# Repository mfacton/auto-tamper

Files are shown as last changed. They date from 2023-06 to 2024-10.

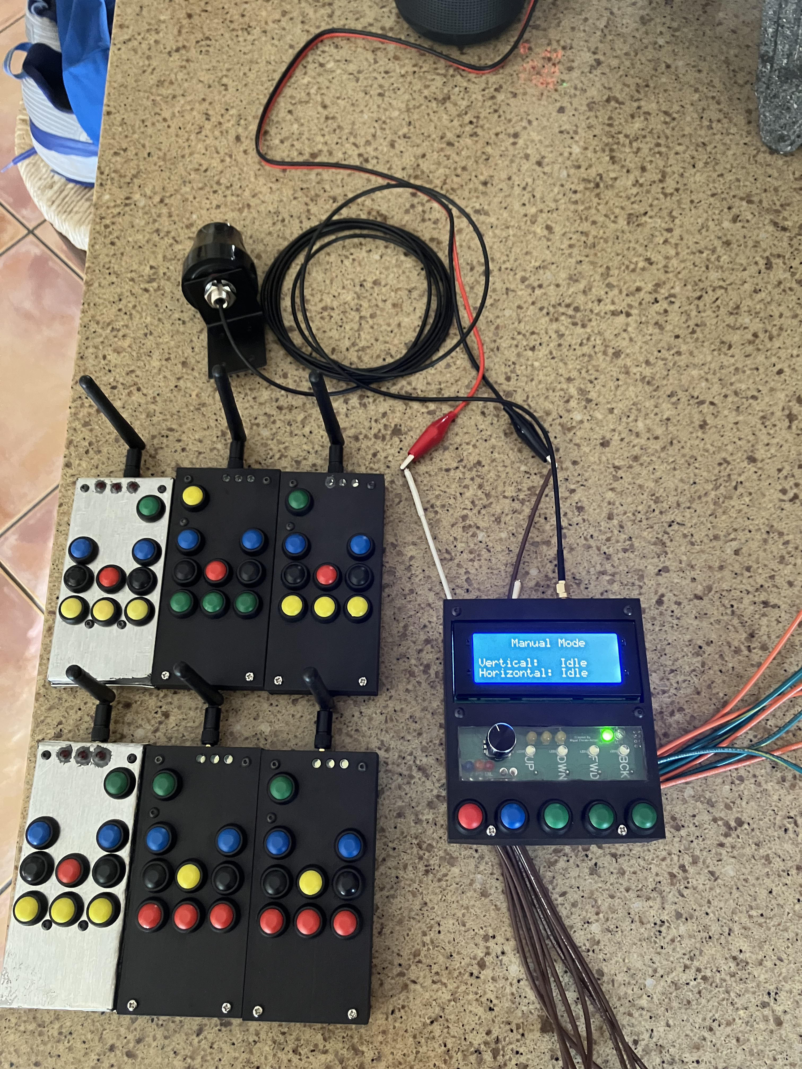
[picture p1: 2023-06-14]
project.jpg

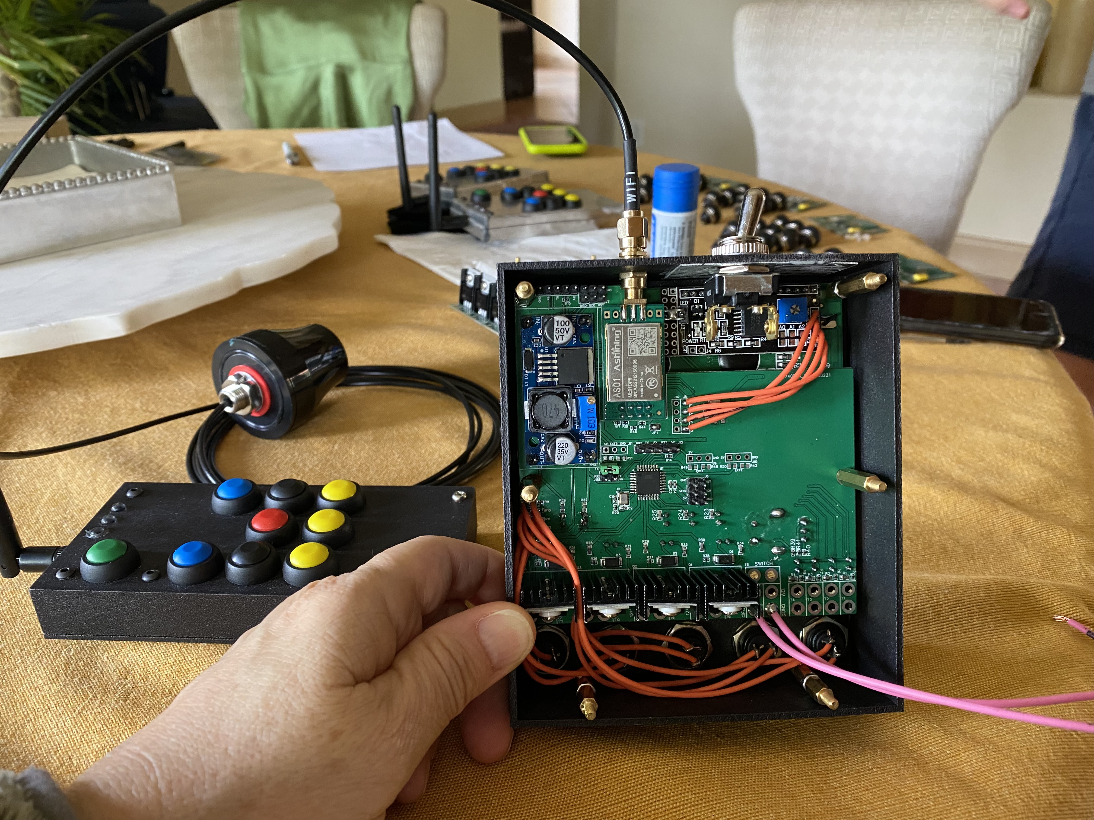
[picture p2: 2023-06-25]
system3/module.jpg

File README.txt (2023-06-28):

This is an autotamper system which includes a module that can be installed onto a module builder as well as remotes for long distance control.
The buttons on the module builder are in order STOP, EDIT, PROG1, PROG2, PROG3

NOTE:
Circuit board files are json files which are openable through the EasyEDA design software.
Both SPI and UART can be accomplished using an Arduino Uno board.
To use SPI, connect pins GND, 3.3V, 10-RESET, 11-MOSI, 12-MISO, 13-CLK.
Also use a voltage Bi-Directional Logic Level Converter so the 5V Arduino Uno signals will not harm the 3V circuit.
To use UART, remove the DIP chip from the Arduino Uno and connect GND, 5V, RESET-RESET, RX-RX, TX-TX.

Remote NOTES:
For remote_v3, install MiniCore on the Arduino IDE, then select the Board: ATMega328, BOD 2.7V, No Bootloader, Extrnal 8MHz Clock, LTO Enabled, Variant 328P/328PA, then to upload program, Sketch -> Upload Using Programmer
For remote_v3, the program can be uploaded using the 6 SPI pins, no bootloader required.
For remote_v2, it is necessary to burn the bootloader before soldering the jumper connector near the transmitter.
Afterwards, a program can be uploaded using the UART pins (5V, RESET, RX, TX, GND).

Module NOTES:
Chip A is located near the center of the board and chip B is located underneath the 12V to 5V voltage regulator.
For the module, it is necessary to burn the bootloader on both ATMega328p-au chips before soldering the jumper connector near the transmitter.
To program the chips, use the 5 UART pins and ensure the RX and TX pins between chips A and B are not connected.
After both chips A and B are programmed, you need to jumper or solder the RX pin of chip A to the TX pin of chip B for them to communicate.

Module Wiring:
12V and GND power the module.
There are 4 sensors, F1: the feeler near the cab, F2: the feeler far from the cab, PS: the pressure sensor, and OIL: the low oil switch.
For the four sensors there is a + and - wire, but it shouldn't matter which way it is connected.
There are also 4 coils which control fwd, back, up, down, each having +/- and the polarity doesn't matter.

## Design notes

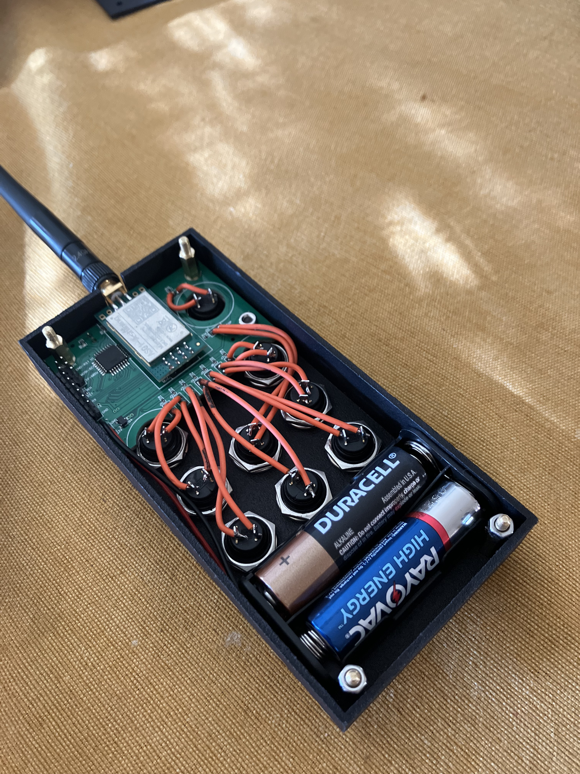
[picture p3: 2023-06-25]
system3/remote_v3/remote.jpg

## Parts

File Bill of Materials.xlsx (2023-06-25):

ITEM | Module | Remote x8 | Source | Unit Price | Total Price
I2C LCD Screen | 1 | 0 | Amazon (https://www.amazon.com/ALMOCN-Display-Interface-Backlight-MEGA2560/dp/B08Z74MSG1) | 8 | 8
5A Inline Fuse | 1 | 0 | Amazon (https://www.amazon.com/HUIQIAODS-Holder-Waterproof-Pigtail-Inline/dp/B08BLHCJBC) | 4 | 4
LEDs | 13 | 3(24) | Amazon (https://www.amazon.com/eBoot-Pieces-Emitting-Diodes-Assorted/dp/B06XPV4CSH) | 0.08 | 2.96
Pin Headers | 22 | 6(48) | Amazon (https://www.amazon.com/Jabinco-Breakable-Header-Connector-Arduino/dp/B0817JG3XN) | 0.01 | 0.7
Buck Regulators | 1 | 0 | Amazon (https://www.amazon.com/Valefod-Efficiency-Voltage-Regulator-Converter/dp/B076H3XHXP) | 1.83 | 1.83
Ceramic Capacitors | 2 | 2(16) | Amazon (https://www.amazon.com/BOJACK-Ceramic-Capacitor-Assortment-Capacitors/dp/B07P8N8BW9) | 0.03 | 0.54
Mosfets | 4 | 0 | Amazon (https://www.amazon.com/BOJACK-IRF520-Transistors-IRF520N-N-Channel/dp/B082J3FNJS) | 0.8 | 3.2
Diodes | 4 | 0 | Amazon (https://www.amazon.com/BOJACK-Schottky-DO-201AD-Electronic-Silicon/dp/B07Q4HYL1P) | 0.24 | 0.96
Buttons | 5 | 9(72) | Amazon (https://www.amazon.com/Waterproof-Momentary-Button-Switch-Colors/dp/B07F24Y1TB) | 0.67 | 51.59
Transcievers | 1 | 1(8) | Amazon (https://www.amazon.com/MakerFocus-nRF24L01P-Transmission-Interface-Anti-Interference/dp/B07QC1SXJ8) | 8.5 | 76.5
Antenna | 1 | 0 | Amazon (https://www.amazon.com/Waterproof-Omni-Directional-Repeater-Wireless-Security/dp/B095JTSQ58) | 15.99 | 15.99
Plexi Glass | 1 | 0 | Ace Hardware | x | x
Rotary Encoder | 1 | 0 | Amazon (https://www.amazon.com/Cylewet-Encoder-Digital-Potentiometer-Arduino/dp/B07DM2YMT4) | 1.78 | 1.78
Switch | 1 | 0 | Ace Hardware | 5.99 | 5.99
Module Circuit | 1 | 0 | JLCPCB (https://jlcpcb.com/) | 24.94 | 24.94
Remote Circuit | 0 | 1(5) | JLCPCB (https://jlcpcb.com/) | 6.14 | 32.06
Module 3D prints | 1 | 0 | JLCPCB (https://3d.jlcpcb.com/) | 32.16 | 32.16
Remote 3D prints | 0 | 5 | JLCPCB (https://3d.jlcpcb.com/) | 21.52 | 107.61
JLCPCB Shipping Total |  |  |  |  | 72.18
M3 Long Bolts | 4 | 3(24) | Ace Hardware | 0.64 | 18
M3 Offsets |  |  | Amazon (https://www.amazon.com/Csdtylh-Male-Female-Standoff-Stainless-Assortment/dp/B06Y5TJXY1) |  | 13.88
Module Duplicate | 1 |  |  | 105.79 | 105.79
Extra Cost = total spent(including old module) - cost per units |  |  |  |  | 250.13
Total |  |  |  |  | 798.63

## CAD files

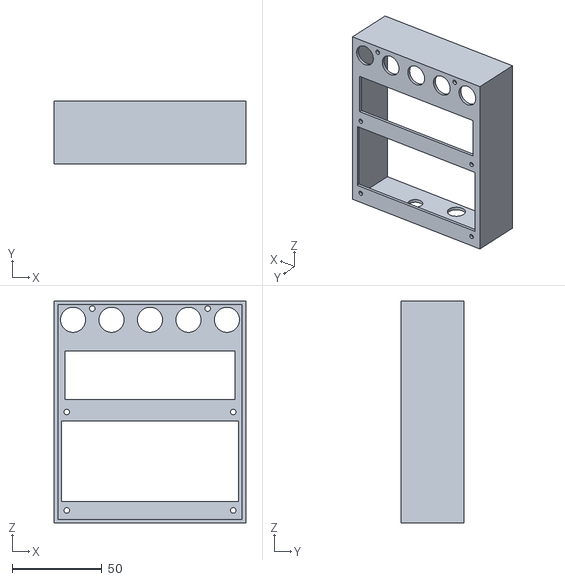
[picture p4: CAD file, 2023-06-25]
system3/module_body.stl
107.0 x 35.0 x 124.0

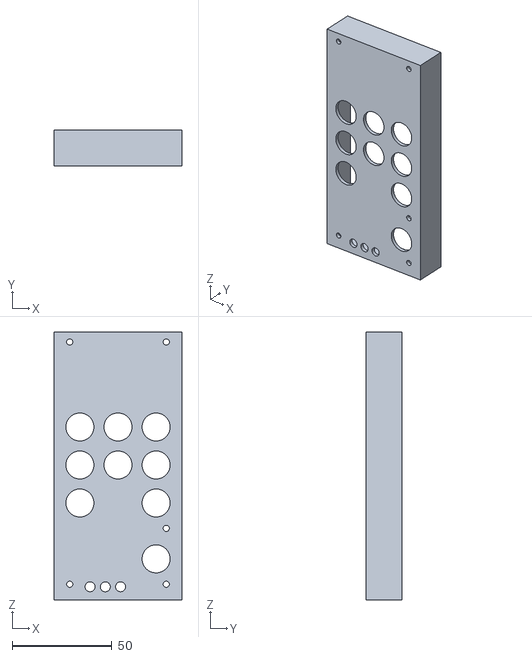
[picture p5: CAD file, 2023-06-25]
system3/remote_v3/remote_body.stl
64.0 x 18.0 x 134.0

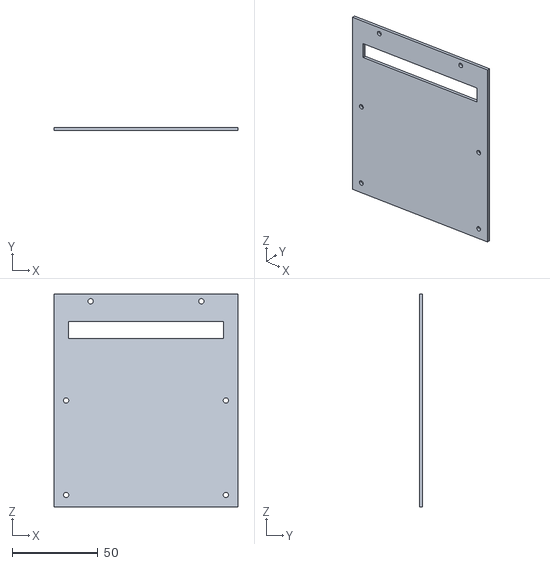
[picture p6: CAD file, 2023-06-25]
system3/module_lid.stl
107.0 x 2.00 x 124.0

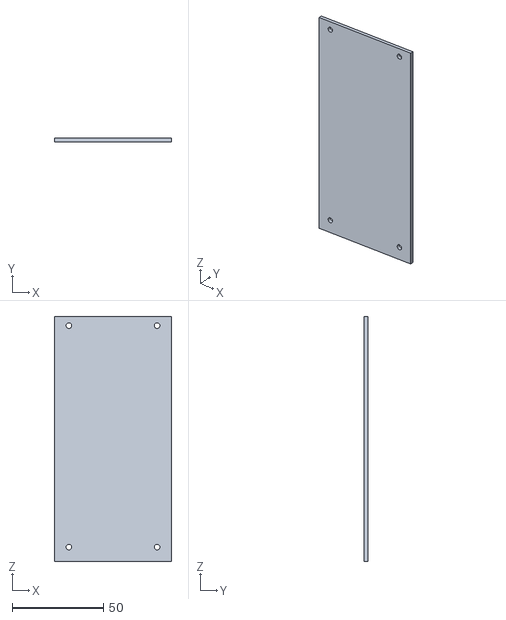
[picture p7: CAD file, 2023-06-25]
system3/remote_v3/remote_lid.stl
64.0 x 2.00 x 134.0

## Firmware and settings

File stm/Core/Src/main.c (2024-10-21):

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
/* Includes ------------------------------------------------------------------*/
#include "main.h"
#include "usb_device.h"

/* USER CODE BEGIN Includes */
#include "modules/movement.h"
#include "modules/input.h"
#include "modules/sensor.h"
#include "modules/memory.h"
#include "modules/display.h"
#include "modules/receiver.h"
#include "modules/LED.h"
#include "control.h"
/* USER CODE END Includes */

I2C_HandleTypeDef hi2c2;

SPI_HandleTypeDef hspi2;

TIM_HandleTypeDef htim2;
TIM_HandleTypeDef htim3;

UART_HandleTypeDef huart1;

void SystemClock_Config(void);
static void MX_GPIO_Init(void);
static void MX_I2C2_Init(void);
static void MX_SPI2_Init(void);
static void MX_USART1_UART_Init(void);
static void MX_TIM2_Init(void);
static void MX_TIM3_Init(void);
/**
  * @brief  The application entry point.
  * @retval int
  */
int main(void)
{
  /* MCU Configuration--------------------------------------------------------*/

  /* Reset of all peripherals, Initializes the Flash interface and the Systick. */
  HAL_Init();

  /* Configure the system clock */
  SystemClock_Config();

  /* Initialize all configured peripherals */
  MX_GPIO_Init();
  MX_I2C2_Init();
  MX_SPI2_Init();
  MX_USART1_UART_Init();
  MX_USB_DEVICE_Init();
  MX_TIM2_Init();
  MX_TIM3_Init();
  /* USER CODE BEGIN 2 */

	HAL_Delay(200);

	Movement_Init();
	Input_Init();
	Sensor_Init();
	Memory_Init(&hi2c2);
	Receiver_Init(&hspi2);
	Display_Init(&hi2c2);

	HAL_Delay(100);

	Control_Init();

  /* USER CODE END 2 */

  /* Infinite loop */
  /* USER CODE BEGIN WHILE */
	while (1) {
		Control_Loop();
    /* USER CODE END WHILE */

    /* USER CODE BEGIN 3 */
	}
  /* USER CODE END 3 */
}

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
/* USER CODE BEGIN 4 */
//every 10 milliseconds
void HAL_TIM_PeriodElapsedCallback(TIM_HandleTypeDef *htim) {
	if (htim == &htim2) {
		Input_Handler();//every 10 milliseconds
	}else{//tim3
		Sensor_Handler_tim();//every 400 microseconds
	}
}

void HAL_GPIO_EXTI_Callback(uint16_t GPIO_Pin) {
	if (GPIO_Pin == NRF_IRQ_Pin) {
		Receiver_Handler();
	}
	else {
		Sensor_Handler_irq(GPIO_Pin);
	}
}
/* USER CODE END 4 */
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


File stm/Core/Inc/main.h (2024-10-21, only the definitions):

#define RE_SW_Pin GPIO_PIN_13
#define RE_SW_GPIO_Port GPIOC
#define RE_CLK_Pin GPIO_PIN_14
#define RE_CLK_GPIO_Port GPIOC
#define RE_DT_Pin GPIO_PIN_15
#define RE_DT_GPIO_Port GPIOC
#define BTN_PRG1_Pin GPIO_PIN_0
#define BTN_PRG1_GPIO_Port GPIOA
#define BTN_STOP_Pin GPIO_PIN_1
#define BTN_STOP_GPIO_Port GPIOA
#define BTN_PRG3_Pin GPIO_PIN_2
#define BTN_PRG3_GPIO_Port GPIOA
#define BTN_PRG2_Pin GPIO_PIN_3
#define BTN_PRG2_GPIO_Port GPIOA
#define BTN_EDIT_Pin GPIO_PIN_4
#define BTN_EDIT_GPIO_Port GPIOA
#define LED_PRG3_Pin GPIO_PIN_5
#define LED_PRG3_GPIO_Port GPIOA
#define LED_PRG2_Pin GPIO_PIN_6
#define LED_PRG2_GPIO_Port GPIOA
#define LED_PRG1_Pin GPIO_PIN_7
#define LED_PRG1_GPIO_Port GPIOA
#define LED_EDIT_Pin GPIO_PIN_0
#define LED_EDIT_GPIO_Port GPIOB
#define NRF_IRQ_Pin GPIO_PIN_1
#define NRF_IRQ_GPIO_Port GPIOB
#define NRF_IRQ_EXTI_IRQn EXTI1_IRQn
#define BOOT1_Pin GPIO_PIN_2
#define BOOT1_GPIO_Port GPIOB
#define NRF_CSN_Pin GPIO_PIN_12
#define NRF_CSN_GPIO_Port GPIOB
#define NRF_CE_Pin GPIO_PIN_8
#define NRF_CE_GPIO_Port GPIOA
#define DBG_TX_Pin GPIO_PIN_9
#define DBG_TX_GPIO_Port GPIOA
#define DBG_RX_Pin GPIO_PIN_10
#define DBG_RX_GPIO_Port GPIOA
#define SIG1_Pin GPIO_PIN_15
#define SIG1_GPIO_Port GPIOA
#define SIG2_Pin GPIO_PIN_3
#define SIG2_GPIO_Port GPIOB
#define SIG3_Pin GPIO_PIN_4
#define SIG3_GPIO_Port GPIOB
#define SIG4_Pin GPIO_PIN_5
#define SIG4_GPIO_Port GPIOB
#define FL1_Pin GPIO_PIN_6
#define FL1_GPIO_Port GPIOB
#define FL1_EXTI_IRQn EXTI9_5_IRQn
#define FL2_Pin GPIO_PIN_7
#define FL2_GPIO_Port GPIOB
#define FL2_EXTI_IRQn EXTI9_5_IRQn
#define PS_Pin GPIO_PIN_8
#define PS_GPIO_Port GPIOB
#define PS_EXTI_IRQn EXTI9_5_IRQn
#define OIL_Pin GPIO_PIN_9
#define OIL_GPIO_Port GPIOB
#define OIL_EXTI_IRQn EXTI9_5_IRQn

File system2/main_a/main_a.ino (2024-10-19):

#include <EEPROM.h>
#include <Wire.h>
#include <LiquidCrystal_I2C.h>

bool editMode = false;
bool autoMode = false;
//independent module
//functions that read sensor inputs
namespace sensors {
  inline void init() {
    DDRD &= 0b11100011;
    DDRC &= 0b11111110;
  }
  inline bool pressure() { //D3
    return !((PIND >> 3)&1);
  }
  bool feeler(uint8_t number) {
    if (number == 0) {//feeler 1
      return !(PINC&1); //C0
    }else{//feeler 2
      return !((PIND>>2)&1); //D2
    }
  }
  inline bool oil() { //D4
    return !((PIND>>4)&1);
  }
}
//independent module
//functions that control movement
namespace movement {
  //coil1 B0 UP
  //coil2 D7 DOWN
  //coil3 D6 FWD
  //coil4 D5 BACK
  inline void init() {
    DDRB |= 0b00000001;
    DDRD |= 0b11100000;
  }
  // bool moving() {
  //   return (PORTD>>5) > 0 || (PORTB&1);
  // }
  inline void up() {
    PORTD &= 0b01111111;
    PORTB |= 0b00000001;
  }
  inline void down() {
    PORTD |= 0b10000000;
    PORTB &= 0b11111110;
  }
  inline void stopUD() {
    PORTB &= 0b11111110;
    PORTD &= 0b01111111;
  }
  inline void forward() {
    PORTD &= 0b11011111;
    PORTD |= 0b01000000;
  }
  inline void backward() {
    PORTD |= 0b00100000;
    PORTD &= 0b10111111;
  }
  void moveFB(uint8_t direction) {
    if (direction) {
      forward();
    }else{
      backward();
    }
  }
  inline void stopFB() {
    PORTD &= 0b10011111;
  }
  inline void stopAll() {
    PORTD &= 0b00011111;
    PORTB &= 0b11111110;
  }
}
//independent module
//functions that control program LEDs
namespace LEDs {
  inline void init() {
    DDRC |= 0b00000010;
    DDRB |= 0b00000110;
  }

  inline void clear() {
    PORTC &= 0b11111101;
    PORTB &= 0b11111001;
  }

  inline void set(uint8_t led) {
    switch (led) {
      case 1: //C1
        PORTC |= 0b00000010;
        break;
      case 2: //B2
        PORTB |= 0b00000100;
        break;
      case 3: //B1
        PORTB |= 0b00000010;
        break;
    }
  }
}
//independent module
//declares some memory locations
//functions that abstract memory managment
namespace mem {
  //0-15 non-used
  //16-63 programs
  //64-127 individual

  constexpr uint8_t height = 0;
  constexpr uint8_t distance = 1;
  constexpr uint8_t delay = 2;
  constexpr uint8_t passes = 3;
  constexpr uint8_t safety = 4;

  uint16_t getVariable (uint8_t address) {
    const uint8_t mappedAddress = address<<1;
    return (EEPROM.read(mappedAddress) << 8) | EEPROM.read(mappedAddress|1);
  }

  void setVariable (uint8_t address, uint16_t value) {
    const uint8_t mappedAddress = address<<1;
    EEPROM.update(mappedAddress, value>>8);
    EEPROM.update(mappedAddress|1, value);
  }

  void reset() {
    for (uint16_t address = 0; address < 256; address++) {
      EEPROM.update(address, EEPROM.read(address+256));
    }
  }

  void setDefaults() {
    for (uint16_t address = 0; address < 256; address++) {
      EEPROM.update(address+256, EEPROM.read(address));
    }
  }
}
//independent module
//intitialize lcd and function to draw text
namespace lcd {
  namespace {
    constexpr char* blankLiteral = "                    ";//20 spaces
    LiquidCrystal_I2C lcd = LiquidCrystal_I2C(0x27, 20, 4);
  }

  inline void init() {
    lcd.init();
    lcd.backlight();
    lcd.noAutoscroll();
    lcd.cursor_off();
    lcd.blink_off();
    lcd.clear();
  }

  inline void print(char* text) {
    lcd.print(text);
  }

  void printText(uint8_t row, uint8_t col, char* text) {
    lcd.setCursor(col, row);
    lcd.print(text);
  }

  void printValue(uint16_t value) {
    char cstr[6];
    ltoa(value, cstr, 10);
    lcd.print(cstr);
    const uint8_t len = strlen(cstr);
    lcd.print(blankLiteral+len+15);
  }

  void printValue(uint8_t row, uint8_t col, uint16_t value) {
    lcd.setCursor(col, row);
    printValue(value);
  }

  inline void printTitle(char* text) {
    uint8_t len = strlen(text);
    printText(0, 10-len/2, text);
  }

  void printLine(uint8_t row, uint8_t col, char* text) {
    const uint8_t len = strlen(text);
    printText(row, col, text);
    const uint8_t start = col+len;
    lcd.print(blankLiteral+start);
  }

  inline void clear() {
    lcd.clear();
  }
}
//display control for edit mode
namespace edit {//7480 989
  namespace {
    constexpr uint16_t DOUBLE_PRESS_TIME = 200;

    constexpr char* scrollIncrements[3] = {"x1", "x50", "x1000"};
    constexpr char* menuLiterals[4] = {"Program 1", "Program 2", "Program 3", "General"};
    constexpr char* programLiterals[8] = {"Height", "Distance Time", "Bottom Delay", "Total Passes", "Safety Timeout", "BACK"};
    constexpr char* generalLiterals[3] = {"Reset", "Set As Default", "BACK"};
    constexpr char* confirmLiterals[2] = {"BACK", "Confirm"};

    constexpr uint8_t confirmRedirects[2] = {0, 0};

    struct page {
      const uint8_t optionLength;
      const uint8_t* redirects;
      const char* title;
      const char** options;
    };

    constexpr page menu = {4, (const uint8_t [4]){1,2,3,4}, "Menu", menuLiterals};
    constexpr page prog1 = {6, (const uint8_t[6]){16,17,18,19,20, 0}, menuLiterals[0], programLiterals};
    constexpr page prog2 = {6, (const uint8_t[6]){32,33,34,35,36, 0}, menuLiterals[1], programLiterals};
    constexpr page prog3 = {6, (const uint8_t[6]){48,49,50,51,52, 0}, menuLiterals[2], programLiterals};
    constexpr page general = {3, (const uint8_t[3]){5, 6, 0}, menuLiterals[3], generalLiterals};
    constexpr page reset = {2, confirmRedirects, generalLiterals[0], confirmLiterals};
    constexpr page setDefaults = {2, confirmRedirects, generalLiterals[1], confirmLiterals};

    constexpr page pages[7] = {
      menu,
      prog1,
      prog2,
      prog3,
      general,
      reset,
      setDefaults
    };

    //menu variables
    uint8_t pageNum;
    uint8_t select;//index of ">"
    uint8_t maxSelect;
    uint8_t view;//index of top selection option
    bool editValue;

    //temp value variables
    uint8_t address;
    uint16_t value;
    uint8_t scroll;//0,1,2 amount to change variable by x1 x50 x1000
    uint16_t increment;//1,50,1000 gets loaded based on "scroll" to save processing

    //-1 no press yet
    //double press to enter
    //single press to change scroll
    long lastPress;

    void initValue(uint8_t valueAddress) {
      editValue = true;
      address = valueAddress;
      value = mem::getVariable(address);
      scroll = 0;
      increment = 1;
      lastPress = 0;

      lcd::clear();
      lcd::printTitle(*(pages[pageNum].options+scroll));
      lcd::printText(1, 0, "Original:");
      lcd::printValue(1, 10, value);
      lcd::printText(2, 0, "Edited:");
      lcd::printValue(2, 8, value);
      lcd::printText(3, 0, "Increment:");
      lcd::printText(3, 11, scrollIncrements[0]);
    }
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

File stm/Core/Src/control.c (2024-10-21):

/*
 * control.c
 *
 *  Created on: Jul 5, 2023
 *      Author: mfact
 */

#include <modules/receiver.h>
#include "main.h"
#include "control.h"
#include "modules/sensor.h"
#include "modules/movement.h"
#include "modules/display.h"
#include "modules/input.h"
#include "modules/LED.h"
#include "modules/memory.h"
#include "modules/menu_config.h"

#include <stdio.h>

//mode variables
static uint8_t mode_edit;
static uint8_t mode_auto;

//buffer for variables in current program
static uint16_t running_variables[8];

//auto variables
static uint8_t pass;
static uint8_t direction;
static uint8_t process;
static uint16_t pass_time;
static uint32_t event_time;
static uint8_t pressure;//for double pressure test

//edit variables
static uint32_t last_press;
static uint8_t edit_value; //bool
static uint8_t page_num;
static uint8_t address;
static uint16_t value;
static uint8_t scroll; //0,1,2
static uint16_t increment;
static uint8_t max_select;
static uint8_t select_option;
static uint8_t view;

//manual variables
static uint8_t last_data;
static uint32_t data_time;
static uint8_t receive_timeout;

//direction literals
static const char *direction_literals[2] = { "back", "fwd " };

//min and max functions
static uint8_t min(int8_t a, int8_t b) {
	if (a < b) {
		return a;
	}
	return b;
}

static uint8_t max(int8_t a, int8_t b) {
	if (a > b) {
		return a;
	}
	return b;
}

void Control_Init(void) {
	mode_edit = 0;
	mode_auto = 0;

	last_data = 0;
	data_time = HAL_GetTick();
	receive_timeout = 1;

	Display_Clear();
	Control_DrawManual();

//	Memory_SetVariable(8, 2000);
//	Memory_SetVariable(9, 2000);
//	Memory_SetVariable(10, 400);
//	Memory_SetVariable(11, 2);
//	Memory_SetVariable(12, 15000);
//
//	//prog2
//	Memory_SetVariable(16, 1600);
//	Memory_SetVariable(17, 1200);
//	Memory_SetVariable(18, 400);
//	Memory_SetVariable(19, 4);
//	Memory_SetVariable(20, 15000);
//
//	//prog3
//	Memory_SetVariable(24, 1300);
//	Memory_SetVariable(25, 500);
//	Memory_SetVariable(26, 500);
//	Memory_SetVariable(27, 6);
//	Memory_SetVariable(28, 15000);
//
//	Memory_WriteBackup();
}
void Control_Loop(void) {
	if (Sensor_State_Oil()) {
		Control_Error("Detected Low Oil");
	}
	if (Input_Ready()) {
		Input_Update();
	}
	if (Input_Read_Latch(INPUT_BTN_EDIT)) {
		mode_edit = !mode_edit;
		LED_Write(LED_EDIT, mode_edit);
		if (mode_edit) {
			Control_StopProgram();
			Control_InitPage(0);
		} else {
			Control_DrawManual();
		}
	}
	if (Input_Read_Latch(INPUT_BTN_STOP)) {
		Control_StopProgram();
	}else if (!mode_edit) {
		if (Input_Read_Latch(INPUT_BTN_PRG1)) {
			Control_RunProgram(1);
		}else if (Input_Read_Latch(INPUT_BTN_PRG2)) {
			Control_RunProgram(2);
		}else if (Input_Read_Latch(INPUT_BTN_PRG3)) {
			Control_RunProgram(3);
		}
	}
	if (mode_edit) {
		Control_EditLoop();
	}
	if (!mode_auto && !receive_timeout && HAL_GetTick() - data_time > 1000) {
		Movement_StopAll();
		Display_PrintLinePosition(2, 12, "Idle");
		Display_PrintLinePosition(3, 12, "Idle");
		receive_timeout = 1;
	}
	if (Receiver_Available()) {
		uint8_t data = Receiver_Read();

		//timeout
		receive_timeout = 0;
		data_time = HAL_GetTick();
		if (data == last_data) {
			goto parse_end;
		}
		//123sfbud

		if (data & 0x1F) {
			if (mode_auto) {
				Control_StopProgram();
				Control_DrawManual();
			}
			if (data & 0x10) {
				Movement_StopAll();
			} else {
				//direction is chosen
				if (data & 0x01) {		// down
					Movement_MoveVertical(MOVEMENT_DOWN);
					if (!mode_edit) {
						Display_PrintLinePosition(2, 12, "Down");
					}
				} else if (data & 0x02) {
					Movement_MoveVertical(MOVEMENT_UP);
					if (!mode_edit) {
						Display_PrintLinePosition(2, 12, "Up");
					}
				} else {
					Movement_MoveVertical(MOVEMENT_VERTICAL_STOP);
					if (!mode_edit) {
						Display_PrintLinePosition(2, 12, "Idle");
					}
				}
				if (data & 0x08) {
					Movement_MoveHorizontal(MOVEMENT_FORWARD);
					if (!mode_edit) {
						Display_PrintLinePosition(3, 12, "Forward");
					}
				} else if (data & 0x04) {
					Movement_MoveHorizontal(MOVEMENT_BACKWARD);
					if (!mode_edit) {
						Display_PrintLinePosition(3, 12, "Backward");
					}
				} else {
					Movement_MoveHorizontal(MOVEMENT_HORIZONTAL_STOP);
					if (!mode_edit) {
						Display_PrintLinePosition(3, 12, "Idle");
					}
				}
			}
		} else if (data & 0xE0) {
			if (!mode_edit) {
				if (data & 0x20) {
					Control_RunProgram(3);
				} else if (data & 0x40) {
					Control_RunProgram(2);
				} else if (data & 0x80) {
					Control_RunProgram(1);
				}
			}
		} else if (!mode_auto) {
			Movement_StopAll();
			Display_PrintLinePosition(2, 12, "Idle");
			Display_PrintLinePosition(3, 12, "Idle");
		}
		parse_end: last_data = data;
	}
	if (mode_auto) {
		Control_AutoLoop();
	}
}

void Control_AutoLoop(void) {
	uint32_t current_time = HAL_GetTick();

	if (process == 0) {
		if (event_time == -1) {
			if (Sensor_State_Pressure()) {
				if (pressure) {
					event_time = current_time;
				}else{
					pressure = 1;
				}
			}else if (pressure){
				pressure = 0;
			}
			HAL_Delay(1);//for the double check
		} else if (current_time - event_time
				>= running_variables[MEMORY_DELAY]) {
			process++;
			event_time = current_time;
			Movement_MoveVertical(MOVEMENT_UP);
		}
	} else if (process == 1) {
		if (current_time - event_time >= running_variables[MEMORY_HEIGHT]) {
			Movement_MoveVertical(MOVEMENT_VERTICAL_STOP);
			Movement_MoveHorizontal(direction);
			event_time = current_time;
			process++;
		}
	} else {
		uint8_t next_process = 0;//bool

		uint32_t delta_time = current_time - event_time;

		if (Sensor_State_Feeler(direction)) {
			Sensor_Feeler_Clear(!direction);
			direction = !direction;
			pass_time = 0;
			next_process = 1;
			pass++;

			//draw direction
			Display_PrintTextPosition(2, 16, direction_literals[direction]);

			//draw pauses
			char str[6];
			uint8_t len = sprintf(str, "%u", pass);
			Display_PrintTextPosition(1, 11 - len, str);

			if (pass >= running_variables[MEMORY_PASSES]) {
				if (mode_auto == 3) {
					Control_StopProgram();
					Control_DrawManual();
				} else {
					Control_RunProgram(mode_auto + 1);
				}
				return;
			}
		} else if (pass_time + delta_time >= running_variables[MEMORY_SAFETY]) {
			Control_Error("Safety Timeout");
		} else if (delta_time >= running_variables[MEMORY_DISTANCE]) {
			pass_time += delta_time;
			next_process = 1;
		}

		if (next_process) {
			process = 0;
			Movement_MoveHorizontal(MOVEMENT_HORIZONTAL_STOP);
			Movement_MoveVertical(MOVEMENT_DOWN);
			pressure = 0;
			event_time = -1;
		}
	}
}
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

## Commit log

2024-10-19 Organize files
    [module_body.stl, module_lid.stl, remote_body.stl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]
2024-10-21 Add stm32 code

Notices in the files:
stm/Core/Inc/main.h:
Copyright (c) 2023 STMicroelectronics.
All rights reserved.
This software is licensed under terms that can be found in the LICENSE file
